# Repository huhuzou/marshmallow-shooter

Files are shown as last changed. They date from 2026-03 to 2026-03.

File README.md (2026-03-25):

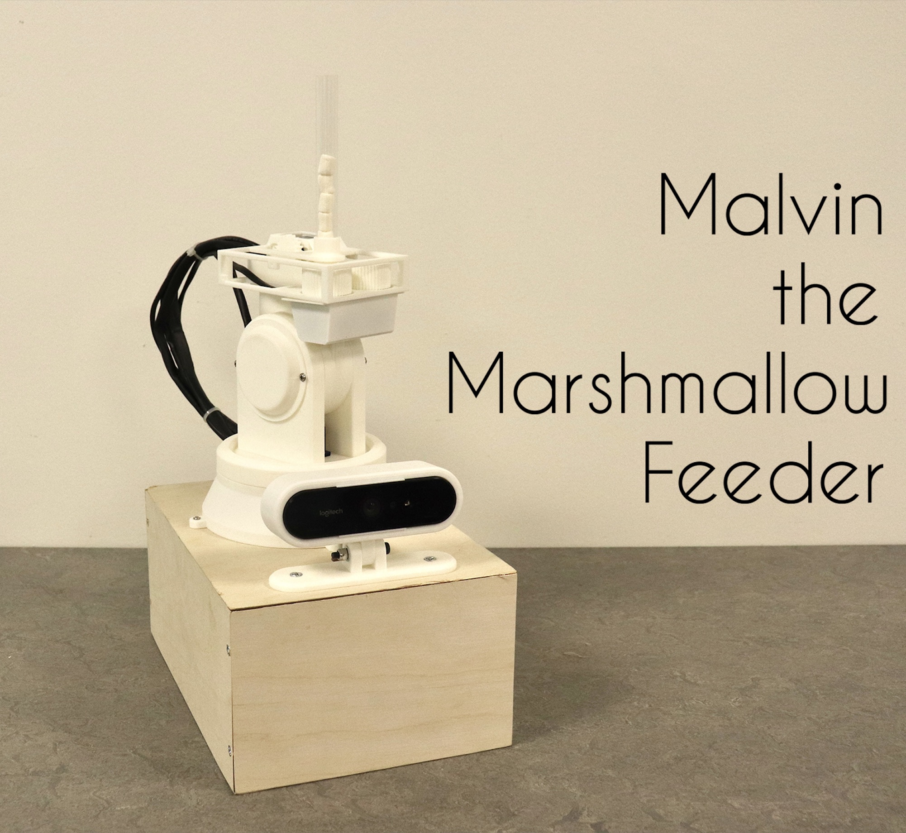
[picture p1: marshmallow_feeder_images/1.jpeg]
Project Overview


## Project Directory

| Folder | Filename | Description |
|---|---|---|
| marshmallow_feeder_cad_file | cam_case.stl<br/>cam_case.stp | Case for the webcam |
| |marshmallow_feeder.stl<br/>marshmallow_feeder.stp | Complete 3D model file for the marshmallow feeder |
| |marshmallow_feeder_arm.stl<br/>marshmallow_feeder_arm.stp | 3D model file for the arm of the marshmallow feeder |
| |marshmallow_feeder_base.stl<br/>marshmallow_feeder_base.stp | 3D model file for the base of the marshmallow feeder |
| |marshmallow_feeder_head.stl<br/>marshmallow_feeder_head.stp | 3D model file for the head (launch mechanism) of the marshmallow feeder |
| marshmallow_feeder_code | arduino_code/aiming_servos | Arduino sketch that controls two aiming servos based on incoming messages. |
| | arduino_code/feeding_servo_and_motors | An Arduino sketch that controls two DC motors for launching and one servo for loading, based on incoming messages. |
| | python_code/cam_to_weki.py | Python code which reads facial x and y coordinates from a camera and sends them via OSC messages. |
| | python_code/mouth_detect.py | Python code that reads the mouth open/close state and sends the information directly to Arduino. |
| | python_code/weki_to_arduino.py | Python code that listens for OSC messages from Wekinator and converts them into serial messages for Arduino. |
| wekinator_file/face_track/WekinatorProject | WekinatorProject.wekproj | A trained Wekinator model that outputs aiming servo angles based on facial coordinates. |

## Overall Concept

The aim was to build a gamified marshmallow launcher that:
1) Tracks a mouth opening/closing
2) Tracks a person's x and y position using 2 servos and an ML algorithm
3) Reloads marshmallows using 1 servo
4) Launches a single marshmallow into the general area of the mouth using 2 DC motors

The project can be viewed as a human snack dispenser that trains humans to catch marshmallows with their mouths.

**Aesthetics**

We wanted the final product to look simplistic, robotic and elegant. Inspired by brutalist architecture, we used white PLA to mimic the minimalist style which focuses on bare materials and structural elements over decorative design. We reinforced the robotic design by separating the machine into distinct parts that each serve their function, with each part exposed so the user can see and understand the mechanical structure whilst using the machine. We used PLA because we could rapidly prototype complex geometries in order to refine the mechanism of the design and iterate on small adjustments and tolerances. It is also a lightweight material, allowing us to keep the movement of the mechanism responsive and smooth.

We made a wooden box to attach the camera and the feeding machine together into one cohesive object. We decided to use 12mm plywood as it provides a good balance between strength, durability and ease of cutting, while keeping the overall weight manageable. The box housed the circuitry and the majority of the wiring to ensure a clean aesthetic. Heat-shrink and crimped connections allowed us to make the wires and connections neater and stronger, whilst ensuring repeatable connection and disconnection during debugging and ML training.

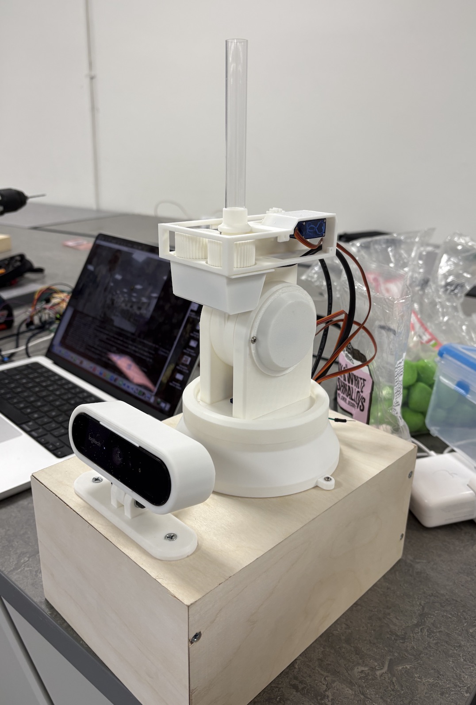
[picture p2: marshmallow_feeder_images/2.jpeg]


**The final design after heat-shrink and cable management:**

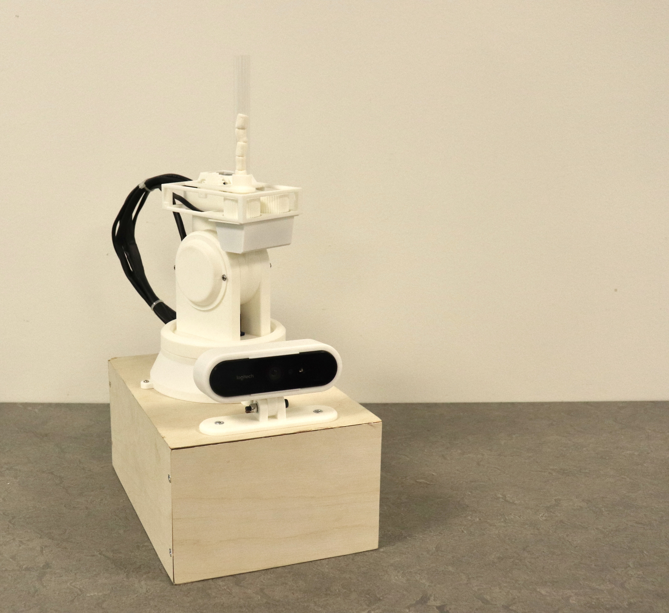
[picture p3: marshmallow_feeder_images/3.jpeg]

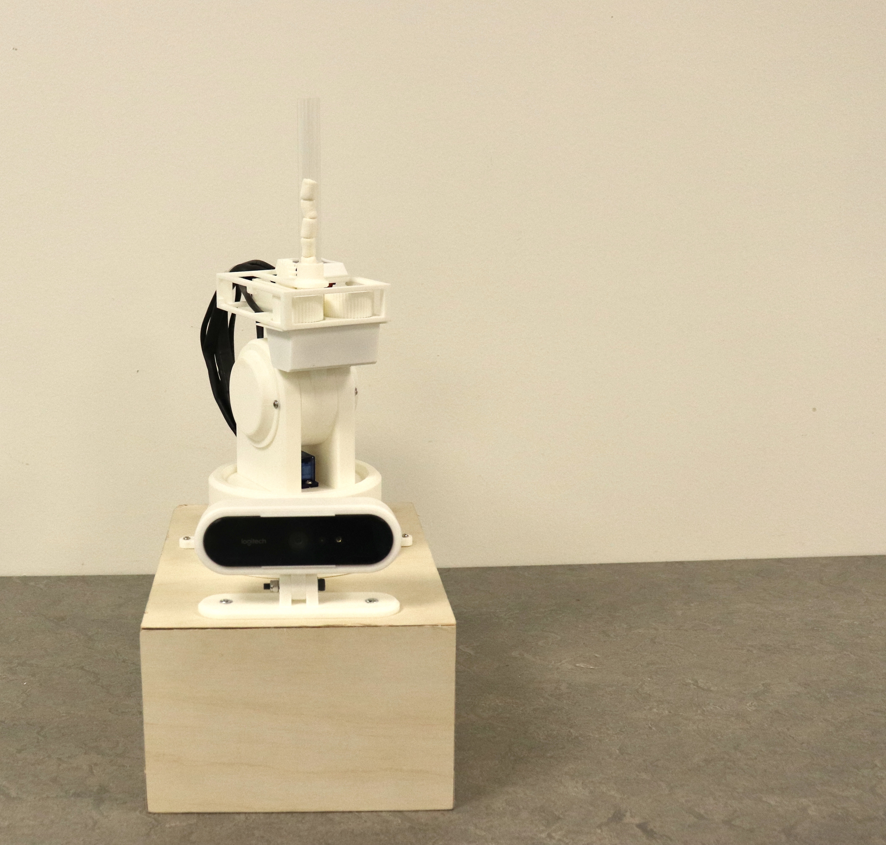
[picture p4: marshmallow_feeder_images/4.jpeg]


## Mechanical Design

Using the mechanism of controlling 4 servos to make a robotic arm move, we simplified the robotic arm into a structure that moves in the x and y directions using 2 servos. The rest of the marshmallow launcher's mechanism was inspired by baseball pitching machines, working by constantly rotating two motors in opposite directions in order to accelerate the marshmallow. Once a 'mouth open' event is detected by the camera tracking, a pinion gear controlled by a servo drives a rack gear forwards, pushing a marshmallow into the gap between the two motors for propulsion out of the device. In parallel, the x and y servos track the person's face position, delivering the marshmallow into the person's general mouth area. This exceeds the performance of the original robot arm by serving the purpose of aiming and launching, which the original arm is not capable of performing.

**Catapult system**

We experimented with a catapult launching mechanism, prior to the baseball pitching mechanism we have implemented into our design. We decided not to continue with the catapult, as it would take up more space and did not provide adequate acceleration and accuracy. The mechanism worked by stretching 2 springs and placing a backboard behind two servos, once a button is pressed, the two servos turn and the backboard is released forward as the 2 springs tighten and move towards the slit in the design.

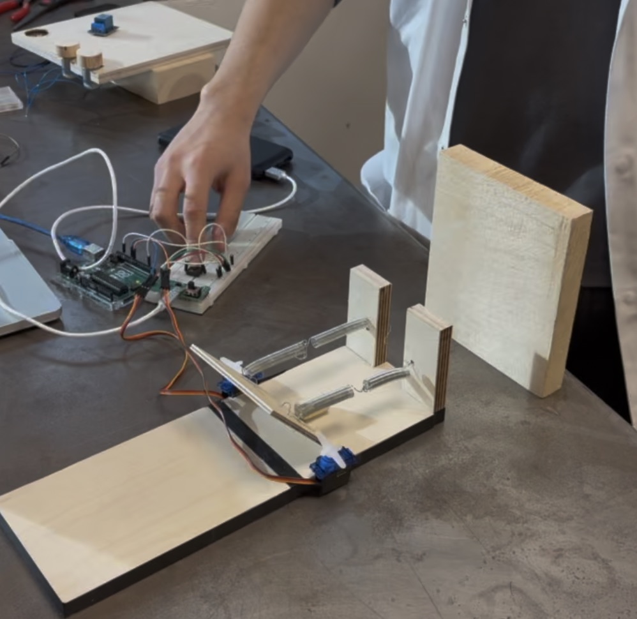
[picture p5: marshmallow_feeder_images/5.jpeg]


**Baseball pitching mechanism (2 power supplies)**

With the baseball pitching mechanism, we first made it work with the use of 2 power supplies - one for each switch. We shortly realised that we do not need to power the 2 motors separately and so we altered the circuit so that both motors can be powered by the same power supply. 

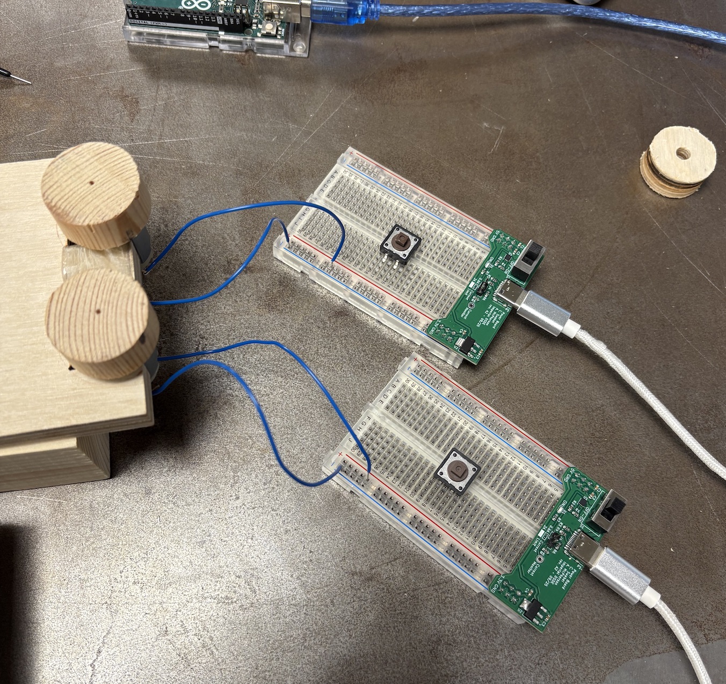
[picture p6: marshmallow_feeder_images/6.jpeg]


**Baseball pitching mechanism (1 power supply) with adjustable distance**

We built a wooden structure to support the DC motors where the relative distance between the motors could be adjusted, allowing us to determine the ideal distance between the acceleration wheels. 

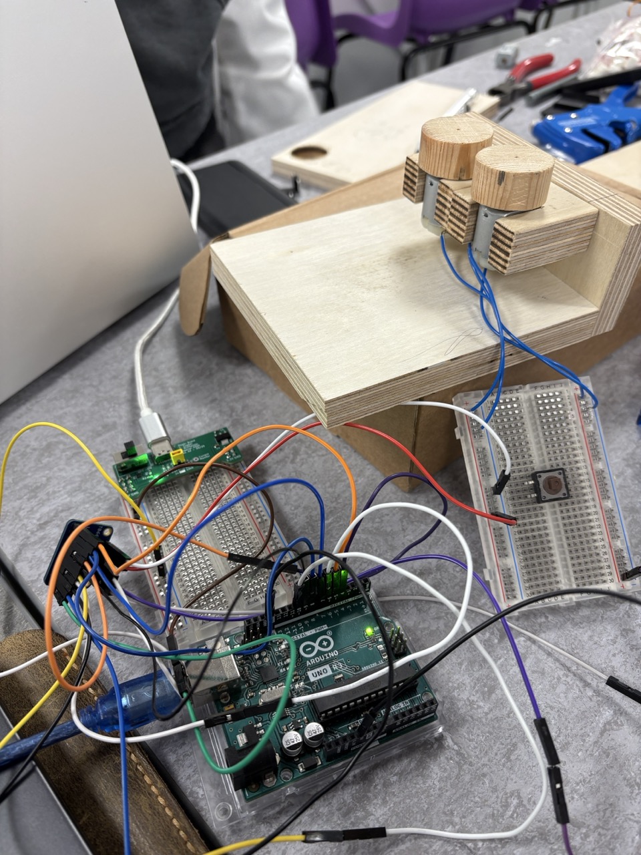
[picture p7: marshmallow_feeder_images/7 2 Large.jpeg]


**Feeding system with acrylic pipe, rack and pinion marshmallow engagement mechanism**

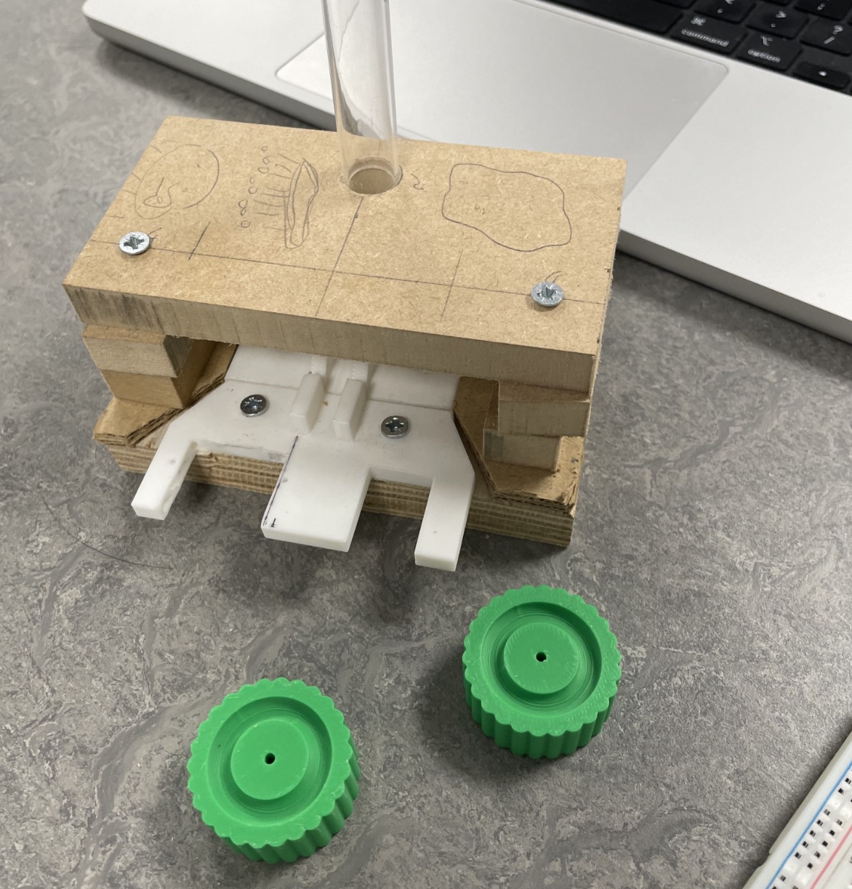
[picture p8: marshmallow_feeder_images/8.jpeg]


The body of the device was developed from the ground up in Rhino, taking into account the dimensions of the servos, motors, feeder tube, etc. Based on our wooden prototypes, we incorporated the elements we had tested, such as the propulsion wheels, feeding system and feeding tube.

One clear tube (ID 11mm, OD 13mm, acrylic tubing) was added to aid the reloading mechanism. Marshmallows fit snugly into the tube and enter a slot in which the rack gear can push the marshmallow through the two rotating motors.

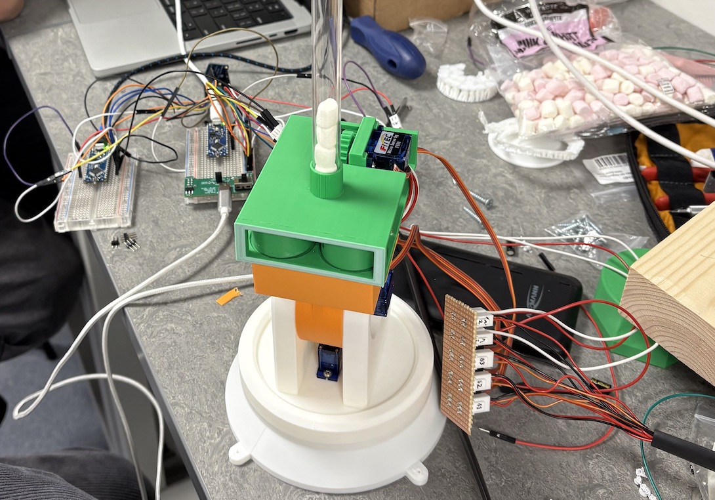
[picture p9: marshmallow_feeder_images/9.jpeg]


We then 3D printed the baseball pitching mechanism in alignment with our aim for a robotic design. PLA is less dense than wood and we wanted the prototype to be as light as possible so the servos can move it more easily according to the power output of the servos. 

First 3D printed prototype (green PLA, with 2 slits to slide in the 2 motors with gears attached)

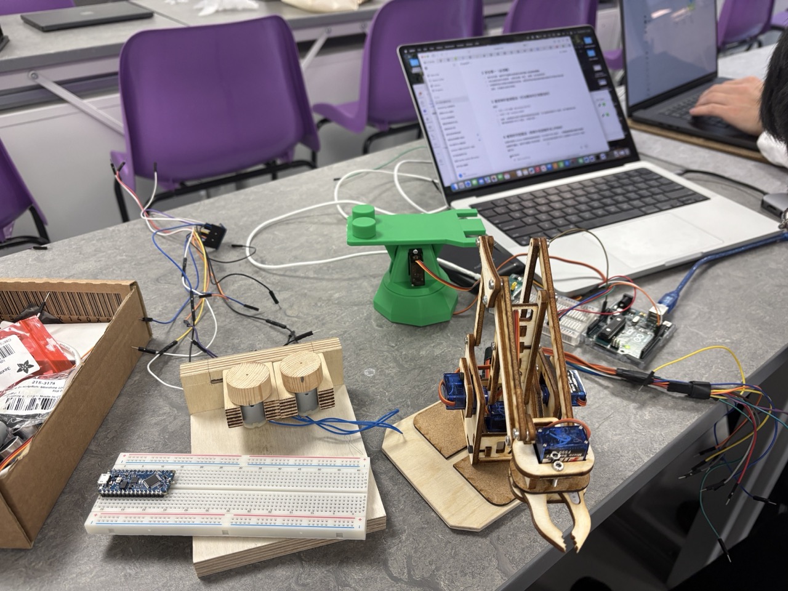
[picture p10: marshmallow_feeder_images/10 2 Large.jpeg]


**Laser pointer (later eliminated)**

We also considered adding a laser pointer to help aim at the mouth during the ML training process but eliminated it due to health and safety concerns.

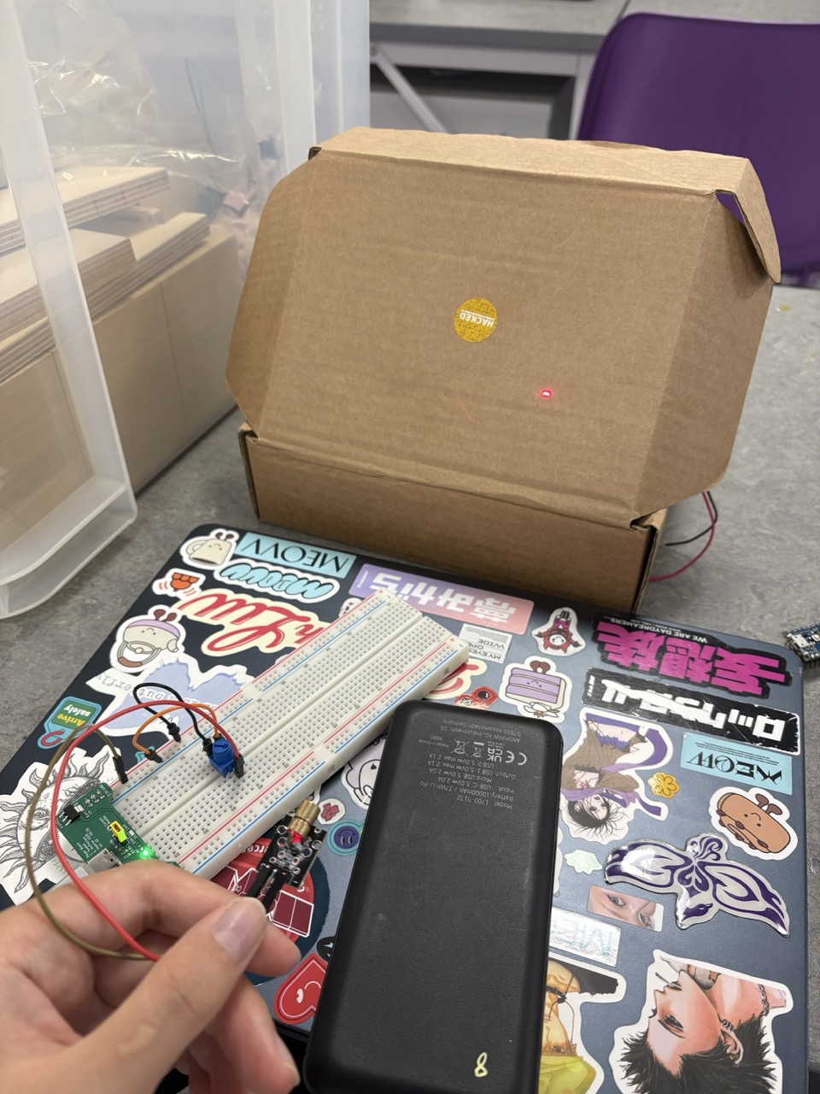
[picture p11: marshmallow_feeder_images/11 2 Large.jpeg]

**Problems with the design**

Launching mechanism weight and friction - the head of the device was too heavy for the servo to move freely. To address this, we cut out sections of the feeder mechanism housing and decreased the surface area of the bearing surfaces in the pivots. This allowed for more efficient power transfer and responsive turning and tilting movements.

**Launching jams and double feeding**

This was addressed by testing various elements. Adjusting the height of the feeding tube in relation to the track the marshmallow was pushed along by the rack gear helped avoid double launches where two marshmallows fell into the feeder chamber. Changing the height and shape of the rack allowed us to block the feeder tube during the launching sequence whilst more reliably presenting the marshmallow to the acceleration wheels. Testing the surface textures of the acceleration wheels helps to increase friction on the marshmallows during launch, allowing the system to reliably grip the marshmallow and also self-clear jams. The top photo shows the wheel with the least friction, as it is smooth, progressing to the wheel with the most friction and grip (bottom photo), which is the one we used in our final project. The middle photo shows the wheel we used; it was better than the top one but it still did not have enough grip for the marshmallows.

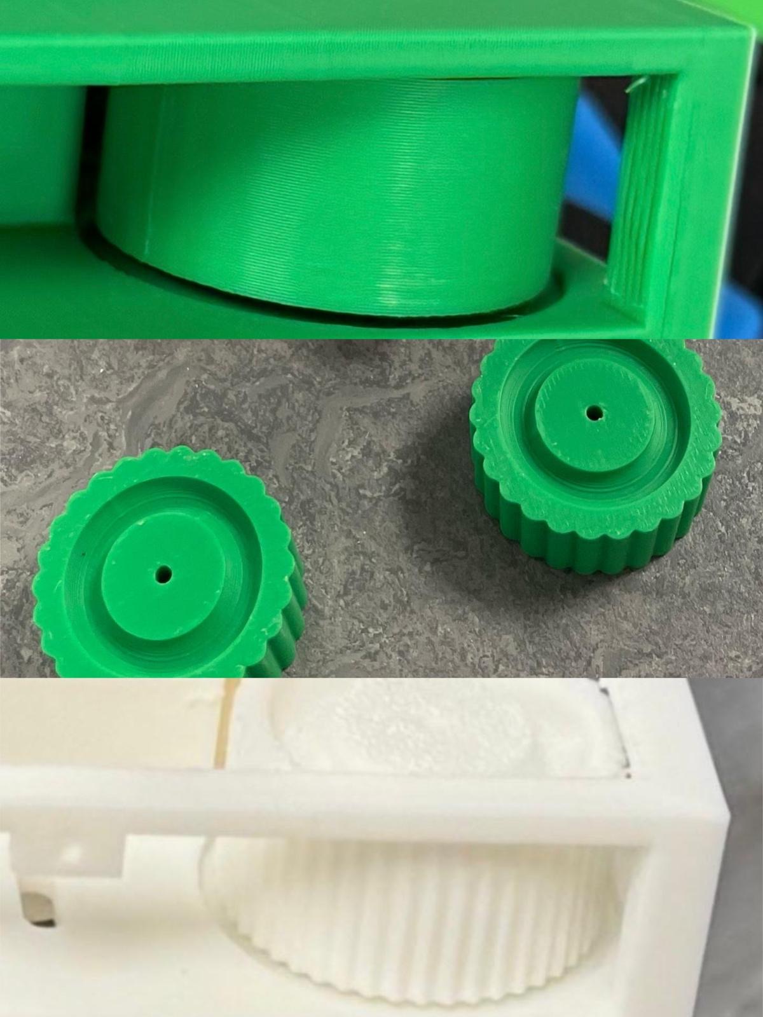
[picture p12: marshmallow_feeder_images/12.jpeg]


## Software design

**Python Script 1 - mouth_detect.py**

This code uses Media Pipe tracking to analyse if a person’s mouth is open or closed based on a video input. It sends values to a local port according to which state is detected.

**Python Script 2 – cam_to_weki.py** 

This code uses Media Pipe to track the xy position of a person’s face based on a video input and sends two values via OSC message that can be processed by Wekinator.

**Python Script 3 – weki_to_arduino.py**

This code converts OSC messages to Serial messages that can be interpreted by Arduino.

**Arduino Sketch 1 – feeding_servo_and_motors**

This sketch controls the DC motors through a dual-H-bridge module and 1 servo that actuates the rack and pinion gears. It receives one input from Python script 1 and runs a launching sequence when it receives a ‘mouth open’ event.

**Arduino Sketch 2 – aiming_servos**

This code controls two servos for the tilting and panning mechanism. It receives a serial code from Wekinator and controls the servos according to the value it receives.

## Hardware design

2 DC motors (3V each)

3 servos (180º)

2 Arduino nanos

4k Logitech webcam + USB-C cable

1 H-bridge

1 5V power board

6 2-pin Molex connectors (male)

9 3-pin Molex connectors (male)

6 2-pin Molex connectors (female)

9 3-pin Molex connectors (female)

12 single core 1mm wires ca. 1m each

1 power bank + USB-A to USB-Micro cable

Acrylic tubing ID 11mm, OD 13mm, 150mm

**Circuit diagram**

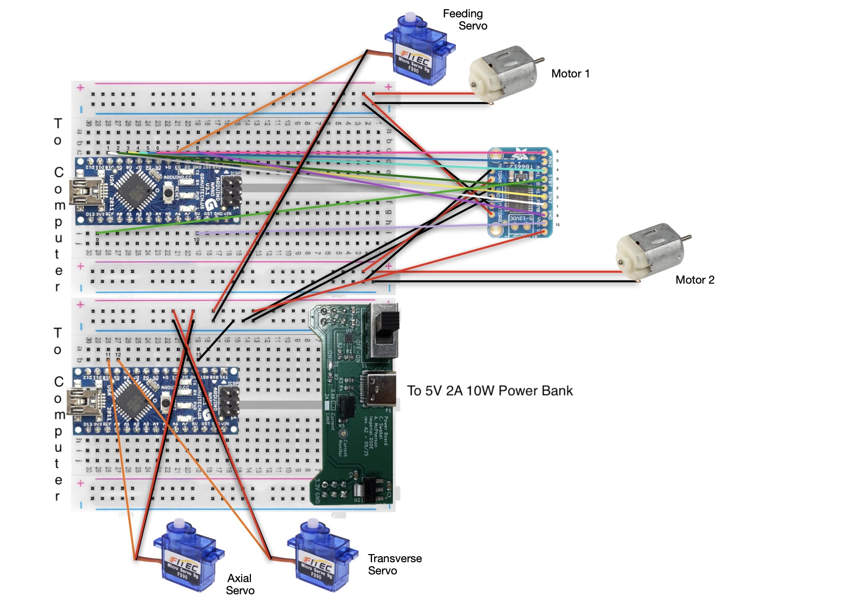
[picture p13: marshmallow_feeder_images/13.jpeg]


To make the circuits in a manner robust enough to withstand the designed movements of the system, the servos and motor wiring were connected to a small junction board mounted to the box via Molex connectors. Molex-terminated cables, heat-shrunk together, connected the junction board to the main circuitry. All remaining components were soldered to a Veroboard, which is housed inside the wooden base.

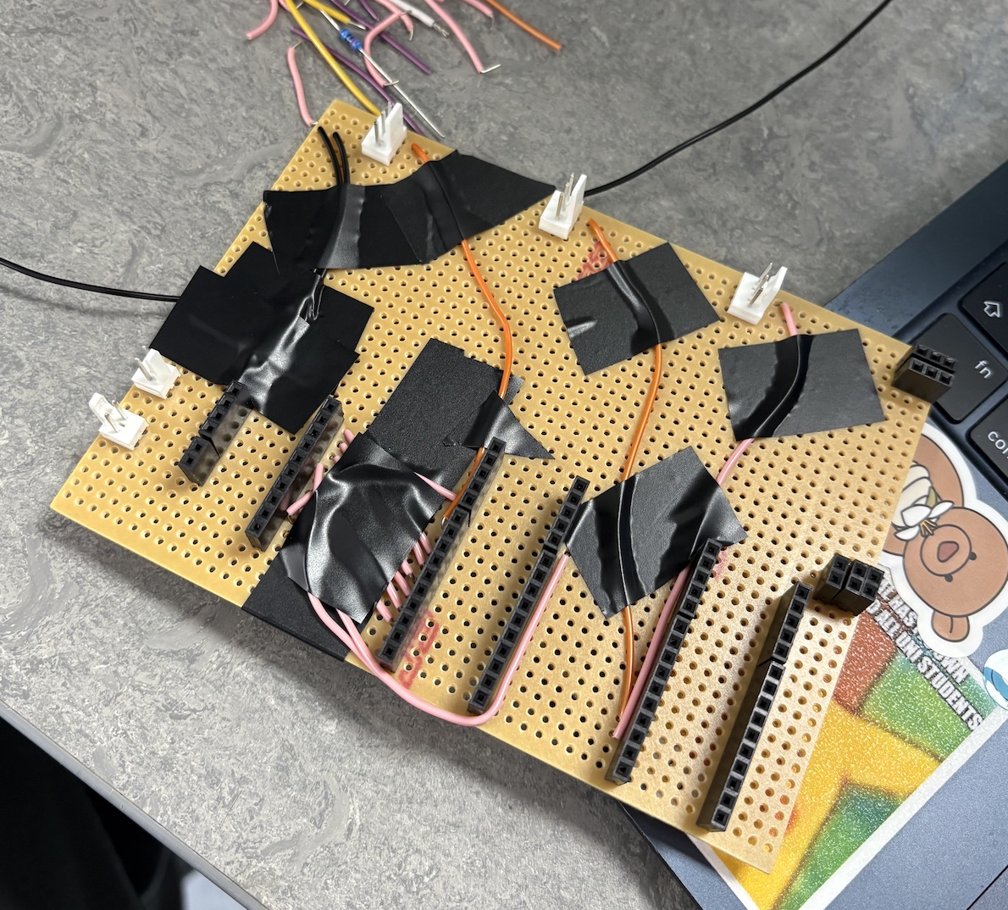
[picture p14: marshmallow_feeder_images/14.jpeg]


This is a diagram displaying the circuit on the Veroboard:

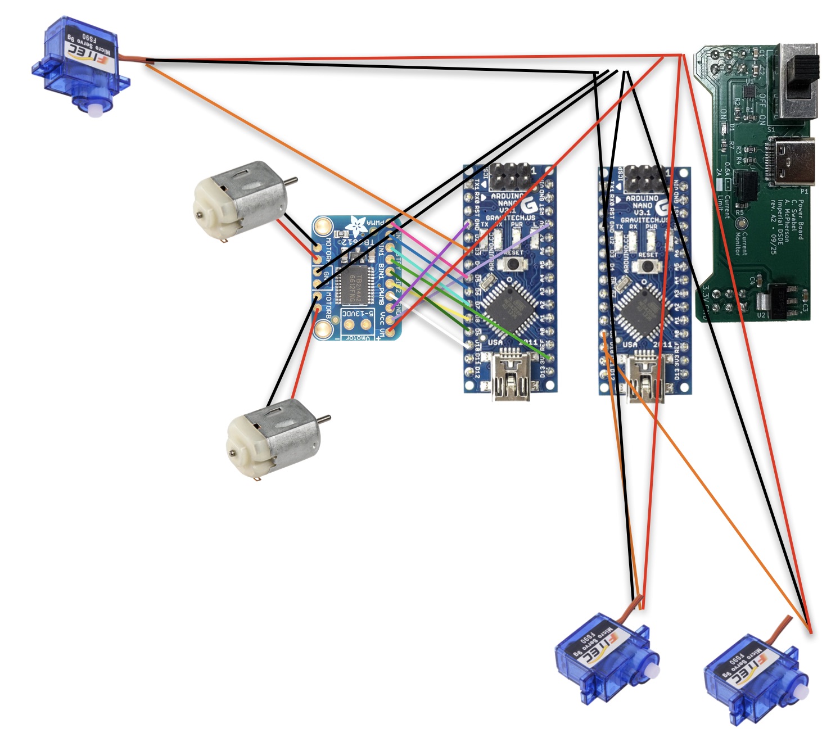
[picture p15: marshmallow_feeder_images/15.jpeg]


To make the connections neater, we also added this Veroboard, which have labels S1, S2, S3, M1 and M2, which stand for servos 1,2,3 and motors 1 and 2, respectively. This is also so we can clearly see how each motor/servo is connected when we rebuild the setup and ensure consistent DC motor polarity.

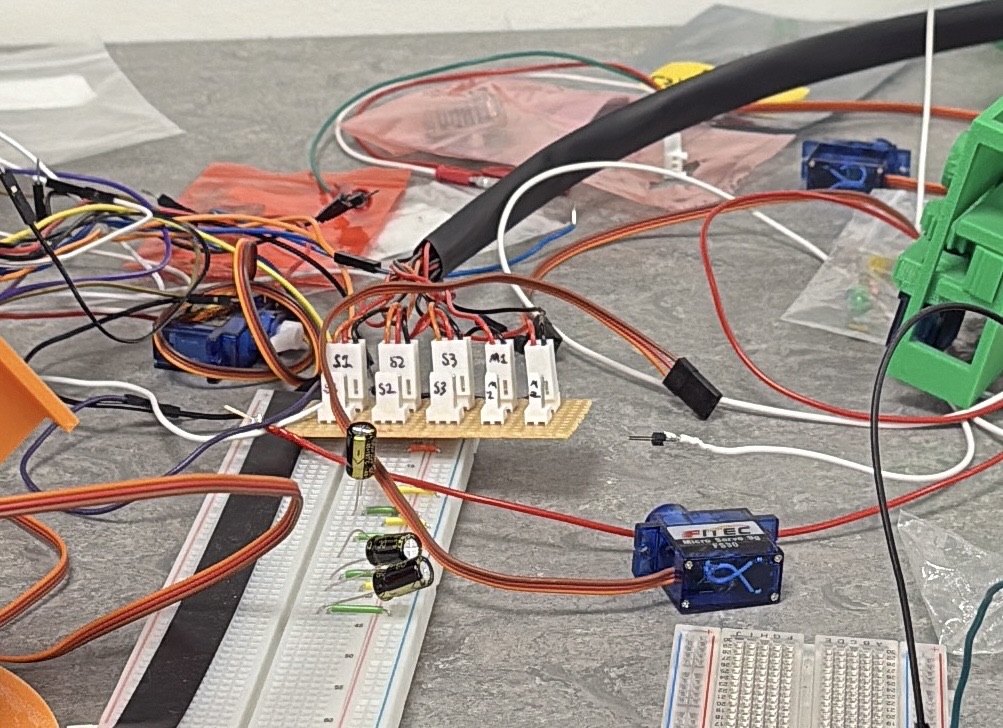
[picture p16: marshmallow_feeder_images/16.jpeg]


## Justification for Using MediaPipe Face Mesh

We are using Python instead of Processing, specifically the MediaPipe Face Mesh package, to monitor the movement of the mouth. MediaPipe Face Mesh uses a CNN-based model. The Convolutional Neural Networks (CNN) are trained to predict 3D face landmarks (468 key points) from a single RGB image. In this case, we used CNN as neural networks are computational models inspired by the human brain. CNN was designed to recognise patterns and make predictions by processing data through interconnected layers of neurons. In a neural network, each neuron receives inputs, applies weights (trains) and produces an output through an activation function, which is a mathematical function applied to the output of a neuron after the weighted sum of its inputs. The CNN method was initially used in image processing, as CNNs are powerful for feature extraction in structured data, which is why it is very powerful for facial recognition in this project. CNNs also use convolutional layers to detect spatial hierarchies, reducing dimensionality and highlighting important features in data, this helps, as all we have to detect is the mouth opening and nothing else.

Other models mentioned in the lecture are not used as KNN (k-Nearest Neighbours) is too slow and not used for image regression and RF (Random Forest) is not suitable for dense landmark prediction. Another commonly used model, GRU (Gated Recurrent Unit), is a recurrent model, so it is not used since Face Mesh processes single frames independently.

## Machine Learning

We evaluated the performance of the trained Wekinator model by testing the dual-servo base's ability to track faces not used during training. The model was trained using face position data (x, y coordinates) recorded from a webcam, with corresponding servo motor positions as output targets. During evaluation, the arm successfully tracked and aimed at new faces in real time, maintaining smooth motion across the frame. Minor deviations (typically within 5–10% of the target position) occurred when faces moved rapidly or when lighting conditions changed significantly. Performance did not depend on the specific person used during training, confirming that the model learned a general mapping for human face positions rather than overfitting to individual features.

The deviation was calculated using the difference between the desired servo position (corresponding to the face’s location) and the actual servo position commanded by the model. The equation used to calculate this was:

Error = (|Predicted Position - Target Position|/Full Range of Servo Motion ) x 100%

The percentage error was computed separately for both the x and y servo axes. Results showed that the errors in both directions followed the same overall trend, with no significant difference between them. This indicates that the model learned a balanced mapping for horizontal and vertical movement, maintaining consistent accuracy across both axes.

## The Future

**Future accomplishment**

The marshmallow can be directly shot in the mouth without the human trying to catch it.

**Further data collection**

The main source of error seemed to be that the face-tracking was distance-dependent. The maximum reliable operating distance was ca. 1.5m. This could be addressed in the future by exploring different models capable of tracking fewer pixels for smaller data points when a person is further away, as well as testing cameras with a longer focal length. Additionally, depth sensors such as ultrasonic or LIDAR sensors could help determine distance to the person in frame and make the training of the launching trajectory more accurate. 

**Potential gain**

A more accurate measurement of how far away the target is can enhance the aim to make launching directly in the mouth more probable.

**Improvement of ML performance**

If we train using Face Mesh and a distance sensor, the system can have metric 3D positions rather than pixel-only estimates. We can also train a motion predictor to aim slightly ahead of the current mouth position.

**Limitations**

Because marshmallows are quite small and the shape is not quite streamlined, aiming it would be harder than other sweets, but due to safety concerns, we are limited to using marshmallows. Although accuracy and aim can be improved immensely with the use of another sensor, it would still not shoot in the mouth exactly all the time. 
Mouth aperture, head micro-movements, breathing, talking, blinking and reflexive movements are highly variable and sometimes unpredictable. Prediction can reduce but not eliminate this source of error.

## Limitations

**Physics**

Reynolds number (Re)
Re = (characteristic speed × characteristic length) / kinematic viscosity
Re = vL/ν
v = speed of the object through the fluid (m/s)
L = characteristic length (m) — for a marshmallow use diameter 
ν = kinematic viscosity of air (m²/s)
Because the Re for marshmallows is so large, it is in the regime where inertial forces dominate and drag behaviour is not linear with speed. Contrary to projectiles, we cannot safely assume a simple parabolic trajectory with constant horizontal speed. Marshmallows vary in shape, mass, elasticity and surface friction. They deform and can tumble unpredictably in flight - this increases aerodynamic uncertainty compared to rigid projectiles. This makes it very hard to predict its flight trajectory, making aiming it even harder. 

If we could also simulate the design, precise values of the metrics can be mathematically calculated so the velocity of the motors can be adjusted based on eg the different masses of the marshmallows during launching. Motors that change speed according to the mass of the marshmallow can also enhance the aim to make launching directly in the mouth more probable. 

**Marshmallows**

We bought two bags of Waitrose & Partners Cooks Ingredients Mini Pink & White Marshmallows (150g) (https://www.waitrose.com/ecom/products/cooks-ingredients-mini-pink-white-marshmallows/479274-816966-816967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). 
We soon realised that the pink marshmallows are slightly larger than the white ones and within the white ones, there are smaller ones and larger ones. We sorted the marshmallows into 3 piles - the smallest ones (left) tend to double-fire and the largest ones (right) tend to jam the machine, hence, we are using the medium sized ones (middle). We determined the size by sliding marshmallows down different sized tubes manually. The smallest ones slid through a tube that is slightly smaller than the one in the actual machine and the medium ones slid through one of the same dimensions as the one used in the actual machine.

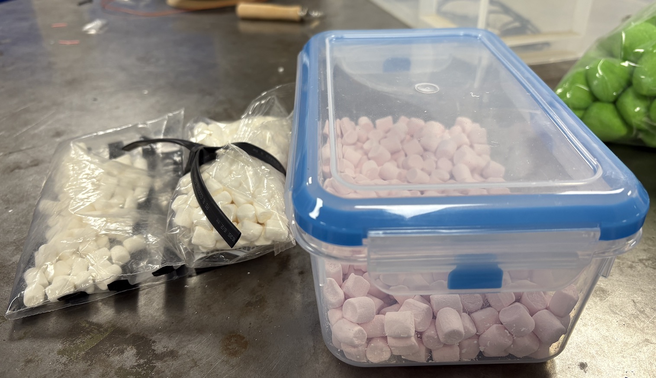
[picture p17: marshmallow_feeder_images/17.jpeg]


## Videos

**## Demo: Marshmallow Shooter in Action**

https://github.com/user-attachments/assets/0494002f-c345-4280-89f7-99e50646e93d

https://github.com/user-attachments/assets/d6a867f2-effc-4d07-804e-cc72e174e246

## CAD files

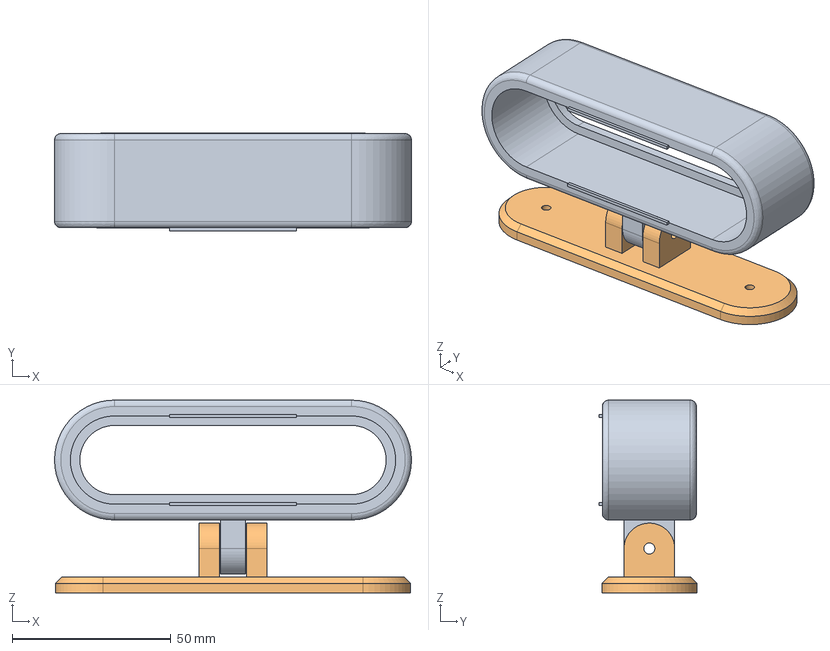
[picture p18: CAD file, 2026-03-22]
marshmallow_feeder_cad_file/cam_case.stp
112.6 x 30.9 x 60.8 mm

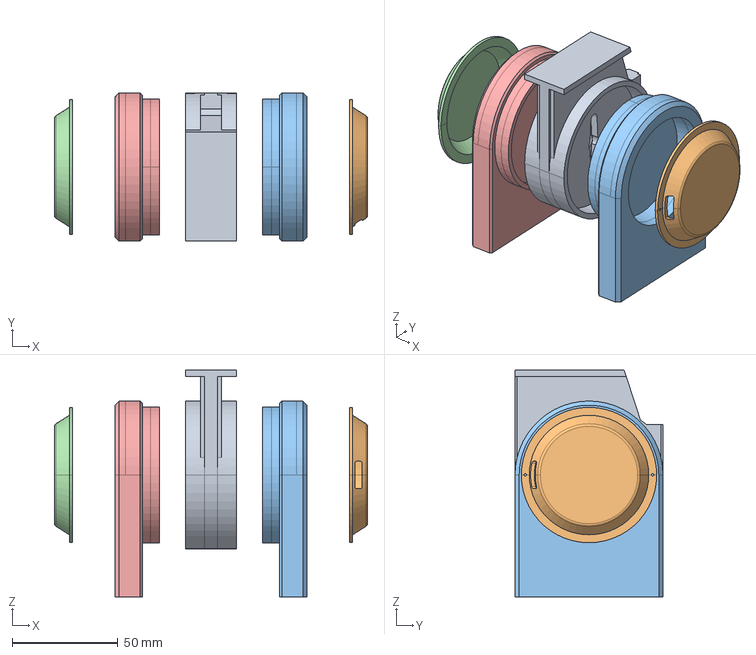
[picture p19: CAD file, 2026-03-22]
marshmallow_feeder_cad_file/marshmallow_feeder_arm.stp
148.0 x 70.0 x 107.2 mm

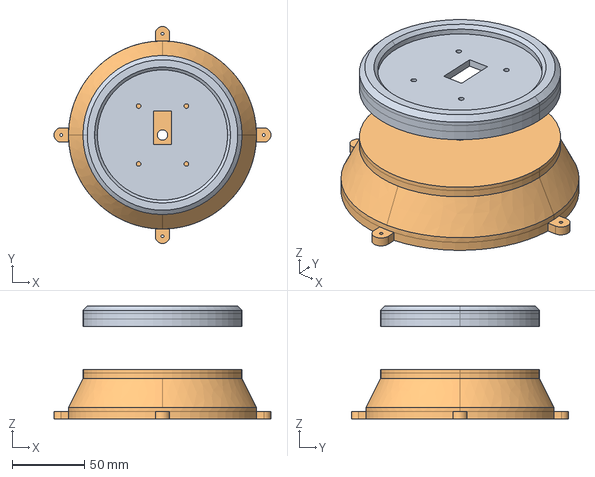
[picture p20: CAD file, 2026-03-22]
marshmallow_feeder_cad_file/marshmallow_feeder_base.stp
150.0 x 150.0 x 78.0 mm

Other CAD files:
marshmallow_feeder_cad_file/cam_case.stl
marshmallow_feeder_cad_file/marshmallow_feeder_arm.stl
marshmallow_feeder_cad_file/marshmallow_feeder_base.stl

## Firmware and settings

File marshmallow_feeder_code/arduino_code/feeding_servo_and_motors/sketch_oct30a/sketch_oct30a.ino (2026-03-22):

#include <Servo.h>

// TB6612 pins
const int AIN1 = 7;
const int AIN2 = 6;
const int PWMA = 5;
const int BIN1 = 9;
const int BIN2 = 8;
const int PWMB = 10;

// Servo pin
Servo mouthServo;
const int SERVO_PIN = 3;

String input = "";

void setup() {
  Serial.begin(115200);

  pinMode(AIN1, OUTPUT);
  pinMode(AIN2, OUTPUT);
  pinMode(PWMA, OUTPUT);
  pinMode(BIN1, OUTPUT);
  pinMode(BIN2, OUTPUT);
  pinMode(PWMB, OUTPUT);

  // motor speed
  analogWrite(PWMA, 255);
  analogWrite(PWMB, 255);

  // motor direction
  digitalWrite(AIN1, HIGH);
  digitalWrite(AIN2, LOW);
  digitalWrite(BIN1, HIGH);
  digitalWrite(BIN2, LOW);

  mouthServo.attach(SERVO_PIN);
  mouthServo.write(90);
}

void loop() {
  while (Serial.available()) {
    char c = Serial.read();
    if (c == '\n') {
      if (input == "OPEN") {
        mouthServo.write(180);
      } else if (input == "CLOSE") {
        mouthServo.write(100);
      }
      input = "";
    } else {
      input += c;
    }
  }
}

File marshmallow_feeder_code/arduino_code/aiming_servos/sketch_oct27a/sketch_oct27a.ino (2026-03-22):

#include <Servo.h>

Servo servo1;
Servo servo2;

void setup() {
  Serial.begin(115200);
  servo1.attach(9);
  servo2.attach(10);
}

void loop() {
  if (Serial.available()) {
    String input = Serial.readStringUntil('\n');
    input.trim();
    int commaIndex = input.indexOf(',');
    if (commaIndex > 0) {
      int val1 = input.substring(0, commaIndex).toInt();
      int val2 = input.substring(commaIndex + 1).toInt();
      val1 = constrain(val1, 0, 180);
      val2 = constrain(val2, 0, 180);
      servo1.write(val1);
      servo2.write(val2);
    }
  }
}
